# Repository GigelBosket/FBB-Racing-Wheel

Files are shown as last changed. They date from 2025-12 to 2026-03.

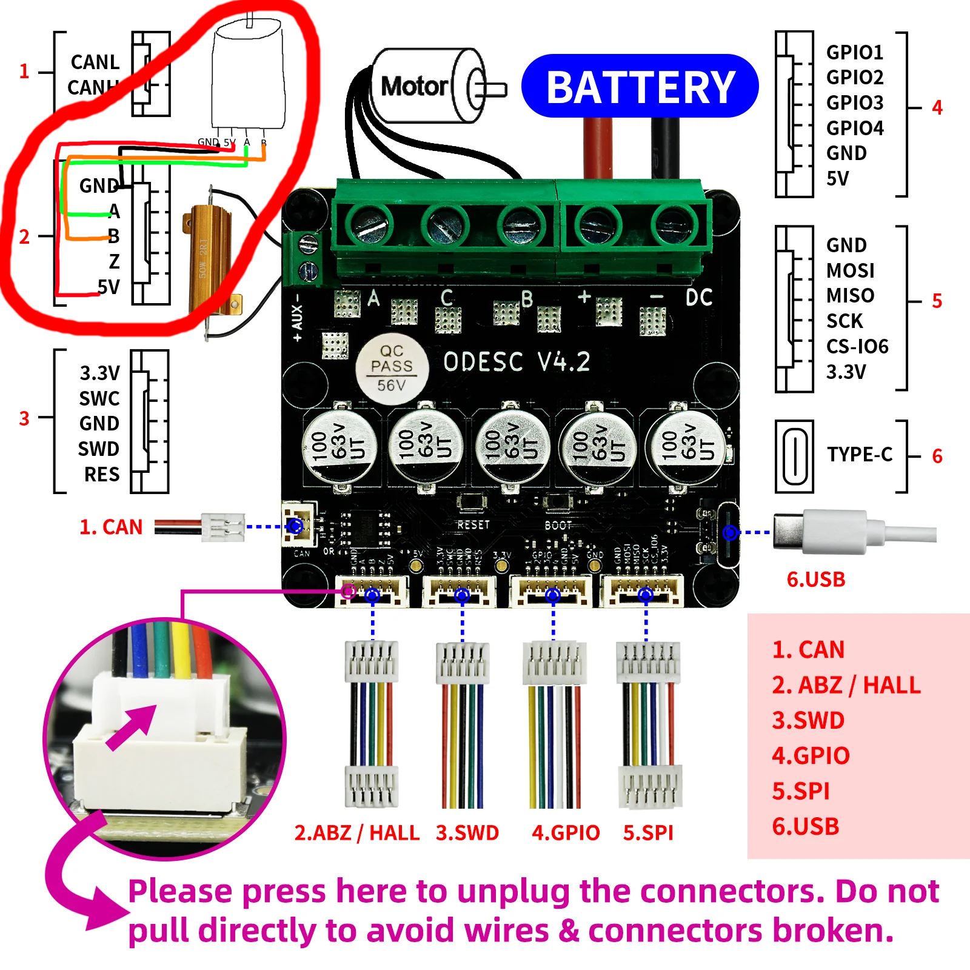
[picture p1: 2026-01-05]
images/ODESC V4.2 diagram.png

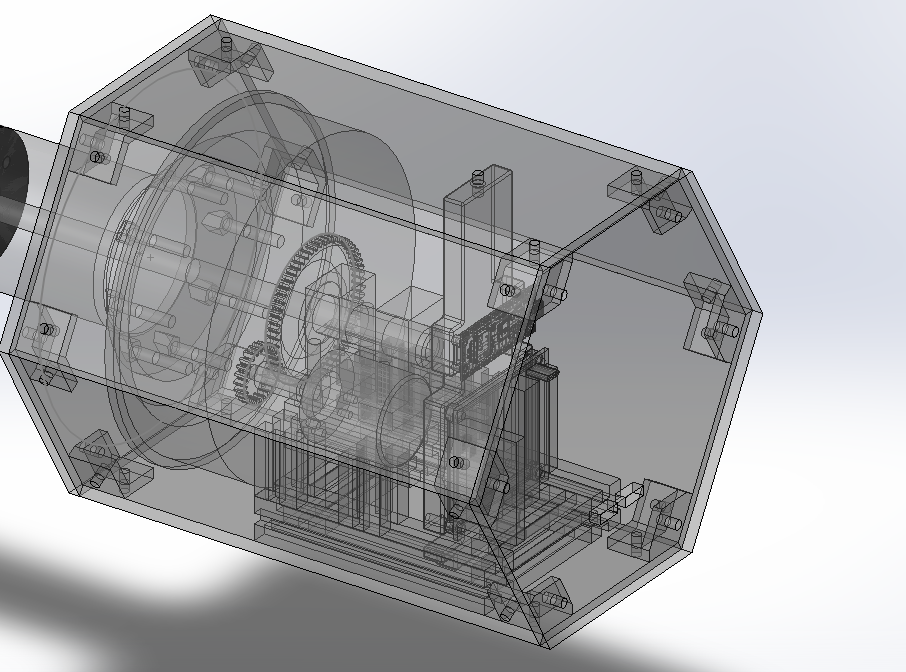
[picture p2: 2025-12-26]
images/Screenshot_1.png

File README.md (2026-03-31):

# FBB-Racing-Wheel
Custom Racing Wheel with Force Feedback containing the wheelbase and steering wheel with the attachments to connect the 2 together. A custom PCB will be used to control the hoverboard motor and read it's position throw a rotary encoder connected to the motor with 2 gears. A Pico 2 is used in the wheelbase to receive data from the wheel(which also has a pico 2) throw SPI protocol. The pico 2 isn't used only for receiving data from the steering wheel, it could also get data from other devices like pedals, shifter, handrbrake and many more. The pico 2 supports up to 6 SPI/I2C connections and also sensors can directly be connected to it's GPIO pins.

The big difference between my racing wheel and others is that mine has direct data transfer throw the magnetic pins from steering wheel to wheelbase which goes in the pc. That means very small latency and no cable twisting all thanks to the magnetic pins (pogo pins) and the slipring. The downside that comes with this is the plastic parts for the high strain parts like the motor extension and the quick release all from plastic(3d printed) but it still should work fine.

I'm making the project so I could inspire others with my design as it's different than most I've seen. And also it's way cheaper than buying a new one with similar specs.

**Specs:**
 - up to 15nm of torque
 - fast response time of 1ms(1000hz)
 - wheel base is  L=20cm, W=20cm(at the corner, max dist) H=17cm.
 - steering wheel is 33cm
 - the 3d printed case for the steering wheel L=16.2cm, W=3.2cm, H=7.5.
 - 12 buttons
 - 5 encoders
 - 1 funcky switch(for easier customization of the car in games/other actions like camera fix position)
 - high precision encoder(for motor)

Wheel final version below
Rendered_model

Wheel base


Close image from the steering wheel face


The back of the steering wheel 


Simple wiring scheme for the Pico 2 of the wheel base to the wires of the slip ring. The image also includes a simple connections from the pico 2 to some sensors if you want to directly connect any sensor to it.


Custom bldc motor driver PCB


PCB image of it's top copper layer


Steering wheel buttons/encoders will be connected to the pico 2 throw a matrix system in which each button is connected to column and row and the pico 2 will send a signal to each column and then wait for output from any of the rows and that's how it will find which buttons got pressed. This matrix system allows the usage of a high number of buttons without haveing a pin for each button. Also a diode will be used to prevent the current from flowing the opposite direction and causing ghosting. The order in which the buttons are connected doesn't matter so I won't include a photo of that. Also I won't add the file for schematic as it's a very simple schematic which isn't linked to other files and it's used to have and idea how the connections work for who doesn't already know(the wires can be connected to others pins and still work fine).Just don't forget to connect it to the pogo pins which then go to the Pico 2 in the wheel base which will process the data, don't forget to wire the pins accordingly for SPI protocol(example above). The pico 2 of the steering wheel is gonna be the slave while the pico in the base is gonna be the master. Slave awaits commands from master.

**Print tips**
So the parts used to connect the motor to the wheel should be printed with 95% infill, the oher parts should be printed with 15-30% infill as they won't have that much strain on them
I m gonna use ASA fillament as it is pretty strong and should do the job well.
Also if you are a total beginer you should download only the stl files as they are the only one needed to print the parts.

I used Raspberry Pi Pico extension in VS code which downloads the SDK for pico and other packages automaticly. If you want to use my code for Pico 2 just git clone my project then open the folder with the code you want to upload on your pico, in VS Code (after installing the extension) and just compile, select port of Pico 2 and upload.

Pico 2:



What you need to wire to the bldc motor driver PCB:
PCB small diagram

| BOM Total | | | Price in us dollars | | | |
|---|---|---|---|---|---|---|
| Material/Product | Quantity | Price per Unit | SubTotal | Shipping | TotalPrice | Link |
| HoverBoard Motor | 1 | 20 | 20 | 5 | 25 | Local Market(OLX.ro) |
| Pico 2 | 1 | 5.5 | 5.5 | 6 | 11.5 | https://www.tme.eu/ro/cart/step/0/order/33780296 |
| SK16 support | 2 | 5.5 | 11 | 5 | 16 | https://www.cnc-kit.ro/cumpara/sk16-suport-ax-16-mm-676 |
| Rotary Encoder 38S6G5-B-G24N | 1 | 11 | 11 | 5 | 16 | https://www.aliexpress.com/item/1005006657099269.html?spm=a2g0o.detail.0.0.48bfnCCMnCCMPD&mp=1 |
| MicroUsb convertor to Usb A | 1 | 0.35 | 0.35 | 0 | 0.35 | https://www.aliexpress.com/item/1005005982662099.html?spm=a2g0o.detail.0.0.771aF986F986OE&mp=1 |
| Usb C convertor to Usb A | 1 | 0.35 | 0.35 | 0 | 0.35 | https://www.aliexpress.com/item/1005005982662099.html?spm=a2g0o.detail.0.0.771aF986F986OE&mp=1 |
| Aluminium Profile 20mm x 1m | 1 | 8 | 8 | 5 | 13 | https://www.automatic.ro/profiluri-de-aluminiu/510-profil-de-aluminiu-20x20-mm-canal-5-tip-item.html |
| M4x10mm Screw | 48 | 0.04 | 1.92 | 0 | 1.92 | https://www.dedeman.ro/ro/surub-cu-cap-cilindric-cu-locas-hexagonal-otel-zincat-alb-din-912-8-8-sw-3-m4-x-10-mm/p/1033735 |
| M4 nuts | 48 | 0.012 | 0.576 | 0 | 0.58 | https://www.dedeman.ro/ro/piulita-hexagonala-din-otel-zincat-alb-din-934-m4/p/6000218 |
| M5 screw(pack of 5) | 1 | 3.62 | 3.62 | 0 | 3.62 | https://www.dedeman.ro/ro/surub-cu-cap-cilindric-cu-locas-hexagonal-otel-zincat-alb-din-912-8-8-m5-x-30-mm-set-5-bucati/p/6014463 |
| M5 nuts | 4 | 0.012 | 0.048 | 0 | 0.05 | https://www.dedeman.ro/ro/piulita-hexagonala-din-otel-zincat-alb-din-934-m5/p/6000211 |
| Slip Ring | 1 | 14 | 14 | 0 | 14 | https://www.aliexpress.com/item/1005007469166149.html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 |
| 6 pin magnetic connector(male and female) | 1 | 2 | 2 | 0 | 2 | https://www.aliexpress.com/item/1005010344872906.html?spm=a2g0o.productlist.0.0.23cd1f3eKvgHZs&mp=1 |
| Power Supply 24v 20A(80%efficiency) | 1 | 39 | 39 | 0 | 39 | https://www.aliexpress.com/item/33051556213.html?spm=a2g0o.cart.0.0.295838daYNvhOv&mp=1 |
| 12AWG Red and Black cable | 1 | 7 | 7 | 0 | 7 | https://www.aliexpress.com/item/1005008617874353.html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 |
| Steering Wheel | 1 | 59 | 59 | 3 | 62 | https://www.aliexpress.com/item/1005005748732216.html?spm=a2g0o.detail.0.0.771aF986F986OE&mp=1 |
| RKJXT1F42001 | 1 | 3.66 | 3.66 | 0 | 3.66 | https://www.aliexpress.com/item/1005006287472896.html?spm=a2g0o.cart.0.0.295838daYNvhOv&mp=1 |
| Push Button | 1 | 2.2 | 2.2 | 0 | 2.2 | https://www.aliexpress.com/item/1005001700262900.html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,scm-url:1007.40050.354490.0,pvid:ea68574a-2666-4e59-a2fa-c057ce48ff6b,tpp_buckets:668%232846%238108%231977&pdp_ext_f=%7B%22order%22%3A%2246%22%2C%22eval%22%3A%221%22%2C%22sceneId%22%3A%2230050%22%2C%22fromPage%22%3A%22recommend%22%7D&utparam-url=scene%3ApcDetailTopMoreOtherSeller%7Cquery_from%3A%7Cx_object_id%3A1005001700262900%7C_p_origin_prod%3A |
| Rotary encoders 15mm shaft(pack of 5) | 1 | 3.7 | 3.7 | 0 | 3.7 | https://www.aliexpress.com/item/32877104625.html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 |
| Knob of rotary encoders (pack of 10( | 1 | 1.4 | 1.4 | 0 | 1.4 | https://www.aliexpress.com/item/1005006995837493.html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 |
| M6 x60mm screw | 6 | 0.17 | 1.02 | 0 | 1.02 | https://www.dedeman.ro/ro/surub-cu-cap-hexagonal-filetat-complet-otel-zincat-alb-m6-x-60-mm/p/6000728 |
| M6 nuts | 6 | 0.032 | 0.192 | 0 | 0.19 | https://www.dedeman.ro/ro/piulita-hexagonala-cu-autoblocare-din-otel-din-985-8-m6/p/6006481 |
| M3 x16mm screw(pack of 20) | 1 | 0.86 | 0.86 | 0 | 0.86 | https://www.dedeman.ro/ro/surub-cu-cap-bombat-amprenta-cruce-cu-piulita-easy-fix-otel-zincat-alb-m3-x-16-mm-set-20-bucati/p/6014509 |
| 1N4148 | 25 | 0.247 | 6.175 | 0 | 6.18 | https://www.tme.eu/ro/details/1n4148-dio/diode-universale-tht/diotec-semiconductor/1n4148/ |
| 28AWG Black Cable | 2 | 0.5 | 1 | 0.7 | 1.7 | https://www.aliexpress.com/item/1005008612186010.html?spm=a2g0o.cart.0.0.295838daYNvhOv&mp=1 |
| 28AWG Red Cable | 2 | 0.5 | 1 | 0 | 1 | https://www.aliexpress.com/item/1005008612186010.html?spm=a2g0o.cart.0.0.295838daYNvhOv&mp=1 |
| PCB(min 5 Q) | 1 | 7 | 7 | 3.12 | 10.12 | |
| PCB BOM(for 1 board) | 1 | 32 | 32 | 9.52 | 41.52 | |
| | | | | | | |
| | | | | | | |
| | | | 243.57 | 42.34 | 285.92 | 

**PCB BOM**
Price is around 23 euros for parts only on LCSC website + other fees.
| Designator | Footprint | Quantity | Value | LCSC Part # |
|---|---|---|---|---|
| 50W RESISTOR | DEGSON DG381-3.5-02P-14-00A(H) | 1 | DEGSON DG381-3.5-02P-14-00A(H) | C5272864 |
| C1, C12, C2, C23, C29, C30, C33, C39, C4, C40, C5, C6, C7, C8 | 402 | 14 | 100nF | C1525 |
| C10, C11, C3, C9 | 402 | 4 | 4.7uF | C23733 |
| C13, C20, C24, C25 | 805 | 4 | 22uF | C711104 |
| C14, C15, C16, C19, C27 | 603 | 5 | 1uF | C15849 |
| C17, C18 | 402 | 2 | 15pF | C161530 |
| C21, C22, C31, C32, C34 | 805 | 5 | 10uF | C440198 |
| C26 | 603 | 1 | 100nF | C1591 |
| C28 | 603 | 1 | 47nF | C1622 |
| C35, C36, C37, C38 | CAP_EEEFK1H221P | 4 | 220uF | C72499 |
| D1 | D_SMC | 1 | SMCJ30A | C4154618 |
| D10 | 402 | 1 | LED | C434446 |
| D2 | D_SMA | 1 | SS14 | C2837270 |
| J1 | USB_C_Receptacle_G-Switch_GT-USB-7051x | 1 | USB_C_Receptacle_USB2.0_16P | C2843970 |
| J3 | JST_SH_BM05B-SRSS-TB_1x05-1MP_P1.00mm_Vertical | 1 | Encoder  Port | C160391 |
| J4 | DORABO DB128V-5.08-5P-GN-S | 1 | DB128V-5.08-5P-GN-S | C2927513 |
| L1 | AOTA-B201610S3R3-101-T | 1 | 3.3uH | C42411119 |
| L2 | VLS6045EX-4R7M-H | 1 | 4.7 uH | C360735 |
| L3 | IND_ETQP4M220KVK | 1 | ETQP4M220KVK | C542324 |
| Q1, Q2, Q3, Q4, Q5, Q6 | TDSON-8-1 | 6 | CSD18532Q5B | C882766 |
| Q7 | SOT-23 | 1 | IRLZ44N(UMW) | C42370423 |
| R1, R5, R6 | 402 | 3 | 33 | C25105 |
| R13, R14, R15, R4, R7 | 402 | 5 | 1k | C11702 |
| R16, R19, R29, R31 | 402 | 4 | 10k | C25744 |
| R18 | 402 | 1 | 100k | C25741 |
| R2, R3 | 402 | 2 | 5k1 | C25905 |
| R20, R21, R22 | 2512 | 3 | 5M1 | C419720 |
| R30 | 402 | 1 | 31k6 | C11463 |
| R8, R9 | 402 | 2 | 27 | C278580 |
| S1 | SW_TL3365AF180QG | 1 | TL3365AF180QG | C2886926 |
| U1 | QFN-48-1EP_7x7mm_P0.5mm_EP5.3x5.3mm | 1 | DRV8323RSRGZR | C545497 |
| U2 | QFN-60-1EP_7x7mm_P0.4mm_EP3.4x3.4mm | 1 | RP2354A | C41378174 |
| U3 | TSOT-23-6 | 1 | AP63203WU | C780769 |
| Y2 | XTAL_ABM8-272-T3 | 1 | ABM8-272-T3 | C20625731 |

The next 2 BOMS are an aproximation for how much for just one of them. It is not 100% accurate

|Wheelbase | | | | |Price in US dollars| |
|---|---|---|---|---|---|---|
|Material/Product |Quantity|Price per Unit|SubTotal |Shipping |TotalPrice |Link |
|HoverBoard Motor |1 |20 |20 |5 |25 |Local Market(OLX.ro) |
|Pico 2 |1 |5.5 |5.5 |6 |11.5 |[link](https://www.tme.eu/ro/cart/step/0/order/33780296) |
|SK16 support |2 |5.5 |11 |5 |16 |[link](https://www.cnc-kit.ro/cumpara/sk16-suport-ax-16-mm-676) |
|Rotary Encoder 38S6G5-B-G24N |1 |11 |11 |5 |16 |[link](https://www.aliexpress.com/item/1005006657099269.html?spm=a2g0o.detail.0.0.48bfnCCMnCCMPD&mp=1) |
|MicroUsb convertor to Usb A |1 |0.35 |0.35 |0 |0.35 |[link](https://www.aliexpress.com/item/1005005982662099.html?spm=a2g0o.detail.0.0.771aF986F986OE&mp=1) |
|Usb C convertor to Usb A |1 |0.35 |0.35 |0 |0.35 |[link](https://www.aliexpress.com/item/1005005982662099.html?spm=a2g0o.detail.0.0.771aF986F986OE&mp=1) |
|Aluminium Profile 20mm x 1m |1 |8 |8 |5 |13 |[link](https://www.automatic.ro/profiluri-de-aluminiu/510-profil-de-aluminiu-20x20-mm-canal-5-tip-item.html) |
|M4x10mm Screw |48 |0.04 |1.92 |0 |1.92 |[link](https://www.dedeman.ro/ro/surub-cu-cap-cilindric-cu-locas-hexagonal-otel-zincat-alb-din-912-8-8-sw-3-m4-x-10-mm/p/1033735) |
|M4 nuts |48 |0.012 |0.576 |0 |0.58 |[link](https://www.dedeman.ro/ro/piulita-hexagonala-din-otel-zincat-alb-din-934-m4/p/6000218) | |
|M5 screw(pack of 5) |1 |3.62 |3.62 |0 |3.62 |[link](https://www.dedeman.ro/ro/surub-cu-cap-cilindric-cu-locas-hexagonal-otel-zincat-alb-din-912-8-8-m5-x-30-mm-set-5-bucati/p/6014463) |
|M5 nuts |4 |0.012 |0.048 |0 |0.05 |[link](https://www.dedeman.ro/ro/piulita-hexagonala-din-otel-zincat-alb-din-934-m5/p/6000211) |
|Slip Ring |1 |14 |14 |0 |14 |[link](https://www.aliexpress.com/item/1005007469166149.html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) |
|6 pin magnetic connector(male and female)|1 |2 |2 |0 |2 |[link](https://www.aliexpress.com/item/1005010344872906.html?spm=a2g0o.productlist.0.0.23cd1f3eKvgHZs&mp=1) |
|Power Supply 24v 20A(80%efficiency) |1 |39 |39 |0 |39 |[link](https://www.aliexpress.com/item/33051556213.html?spm=a2g0o.cart.0.0.295838daYNvhOv&mp=1) |
|12AWG Red and Black cable |1 |7 |7 |0 |7 |[link](https://www.aliexpress.com/item/1005008617874353.html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)
| | | | | | | |
| | | | | | | |
| | | |151.36  |31 |181.37 | |

|Steering Wheel | | | | |Price in us dollars| |
|---|---|---|---|---|---|---|
|Materials/Products |Quantity|Price per Unit|SubTotal|Shipping|Total Price |Links |
|Steering Wheel |1 |59 |59 |3 |62 |[link](https://www.aliexpress.com/item/1005005748732216.html?spm=a2g0o.detail.0.0.771aF986F986OE&mp=1) |
|RKJXT1F42001 Multi-function switch |1 |3.66 |3.66 |0 |3.66 |[link](https://www.aliexpress.com/item/1005006287472896.html?spm=a2g0o.cart.0.0.295838daYNvhOv&mp=1) |
|Push Button Switch with caps(pack of 50)|1 |2.2 |2.2 |0 |2.2 |[link](https://www.aliexpress.com/item/1005001700262900.html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,scm-url:1007.40050.354490.0,pvid:ea68574a-2666-4e59-a2fa-c057ce48ff6b,tpp_buckets:668%232846%238108%231977&pdp_ext_f=%7B%22order%22%3A%2246%22%2C%22eval%22%3A%221%22%2C%22sceneId%22%3A%2230050%22%2C%22fromPage%22%3A%22recommend%22%7D&utparam-url=scene%3ApcDetailTopMoreOtherSeller%7Cquery_from%3A%7Cx_object_id%3A1005001700262900%7C_p_origin_prod%3A)|
|Rotary encoders 15mm shaft(pack of 5) |1 |3.7 |3.7 |0 |3.7 |[link](https://www.aliexpress.com/item/32877104625.html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) |
|Knob of rotary encoders (pack of 10( |1 |1.4 |1.4 |0 |1.4 |[link](https://www.aliexpress.com/item/1005006995837493.html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) |
|M6 x60mm screw |6 |0.17 |1.02 |0 |1.02 |[link](https://www.dedeman.ro/ro/surub-cu-cap-hexagonal-filetat-complet-otel-zincat-alb-m6-x-60-mm/p/6000728) |
|M6 nuts |6 |0.032 |0.192 |0 |0.19 |[link](https://www.dedeman.ro/ro/piulita-hexagonala-cu-autoblocare-din-otel-din-985-8-m6/p/6006481) |
|M3 x16mm screw(pack of 20) |1 |0.86 |0.86 |0 |0.86 |[link](https://www.dedeman.ro/ro/surub-cu-cap-bombat-amprenta-cruce-cu-piulita-easy-fix-otel-zincat-alb-m3-x-16-mm-set-20-bucati/p/6014509) |
|Pico 2 |1 |5.5 |5.5 |0 |5.5 |[link](https://www.tme.eu/ro/details/sc1631/raspberry-pi-sisteme-incorporate/raspberry-pi/raspberry-pi-pico-2/) | |
|1N4148 |25 |0.247 |6.175 |0 |6.18 |[link](https://www.tme.eu/ro/details/1n4148-dio/diode-universale-tht/diotec-semiconductor/1n4148/) |
|28AWG Black Cable |2 |0.5 |1 |0.7 |1.7 |[link](https://www.aliexpress.com/item/1005008612186010.html?spm=a2g0o.cart.0.0.295838daYNvhOv&mp=1) |
|28AWG Red Cable |2 |0.5 |1 |0 |1 |[link](https://www.aliexpress.com/item/1005008612186010.html?spm=a2g0o.cart.0.0.295838daYNvhOv&mp=1) |
| | | | | | | |
| | | | | | | |
| | | |100.21 |3.7 |103.91 | |

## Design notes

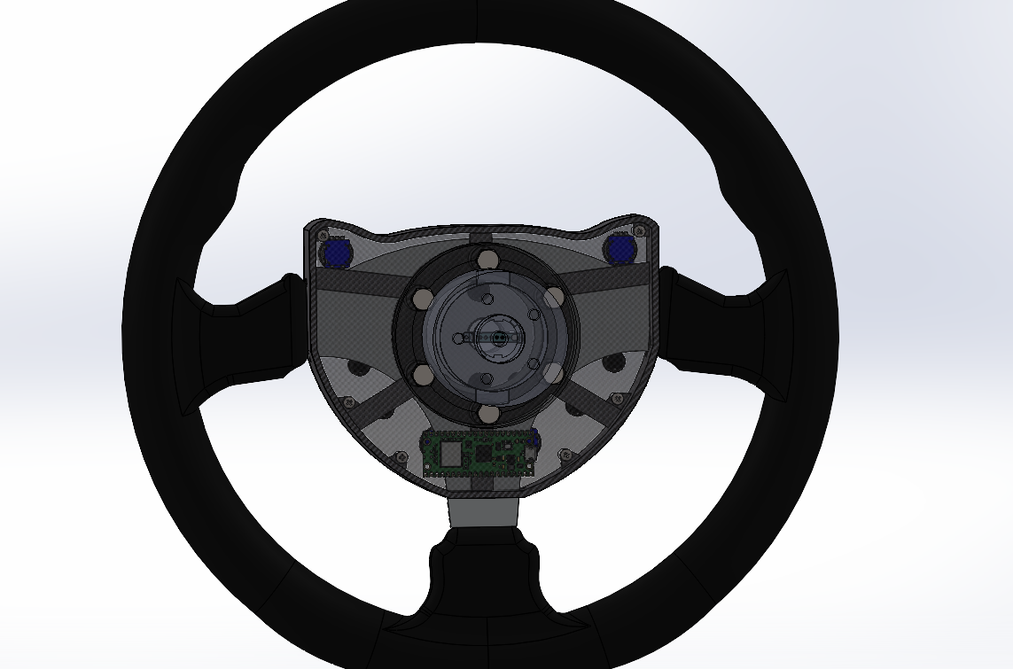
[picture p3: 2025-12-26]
images/Screenshot_3.png

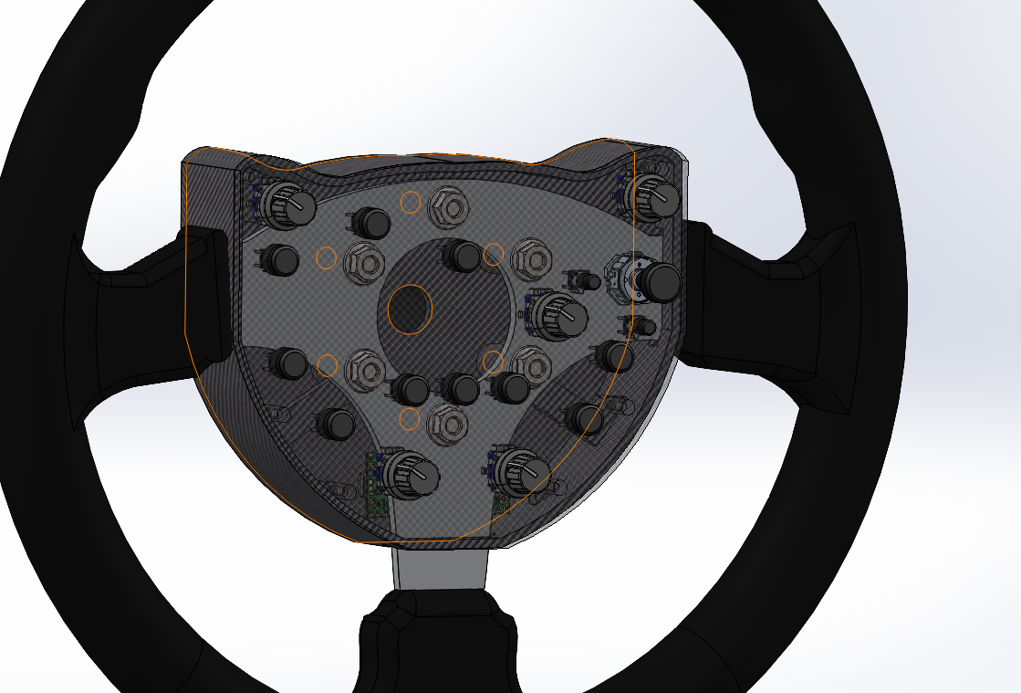
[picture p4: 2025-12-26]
images/Screenshot_2.png

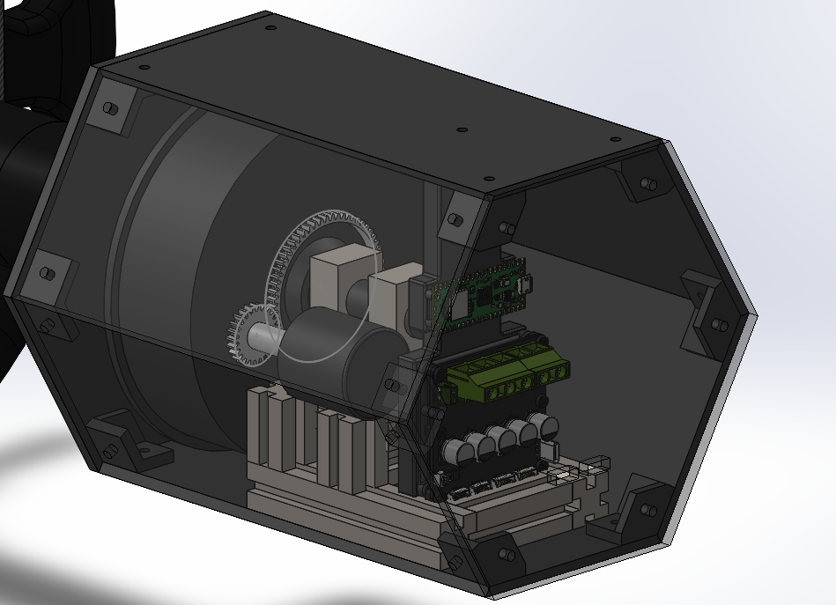
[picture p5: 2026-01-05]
images/Screenshot_4.png

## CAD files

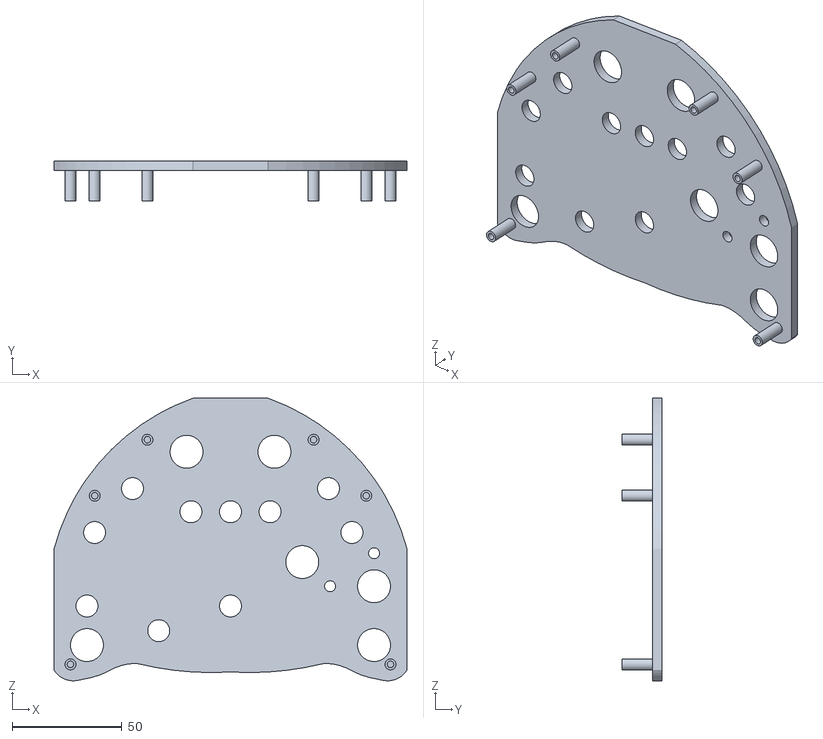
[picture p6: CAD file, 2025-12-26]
CAD/STL/SteeringWheel/Wheel front face.STL
160.7 x 18.2 x 128.7

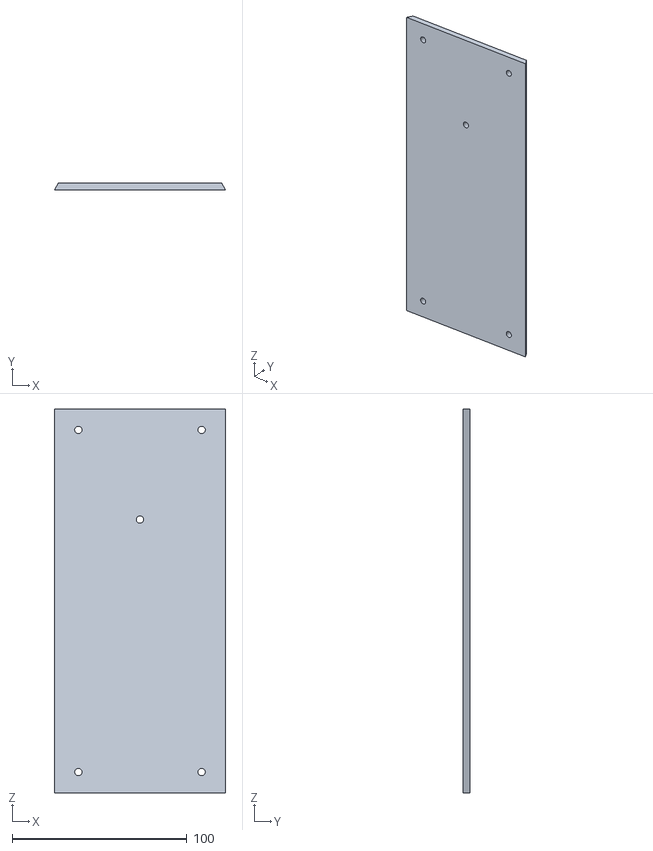
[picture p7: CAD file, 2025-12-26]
CAD/STL/WheelBase/Top plate.STL
98.2 x 4.00 x 220.0

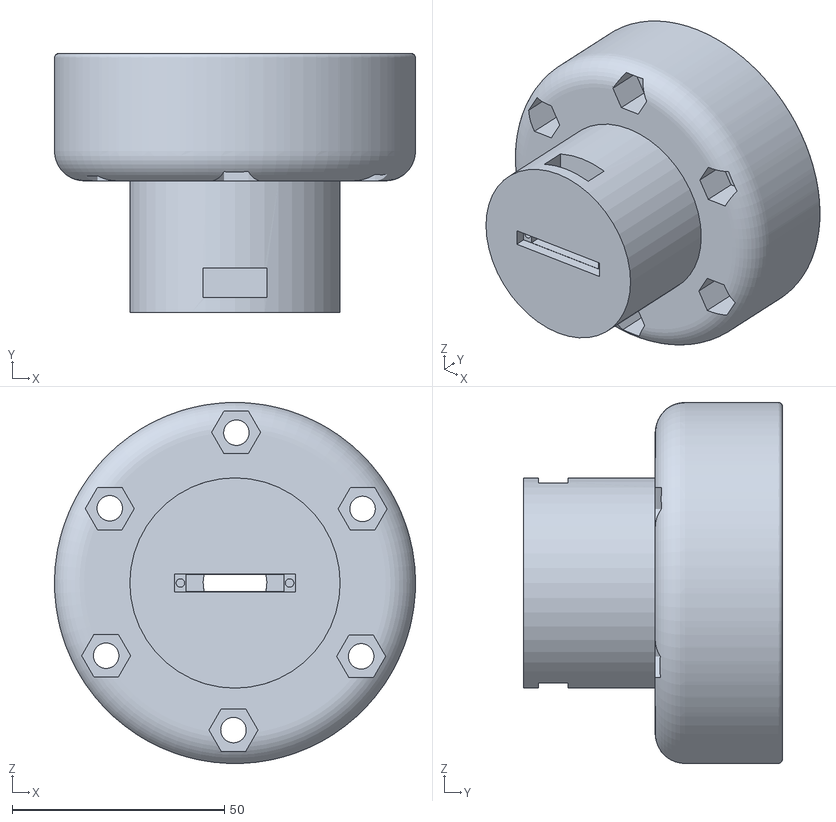
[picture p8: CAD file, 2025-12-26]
CAD/STL/SteeringWheel/wheel attachement.STL
85.0 x 61.0 x 85.0

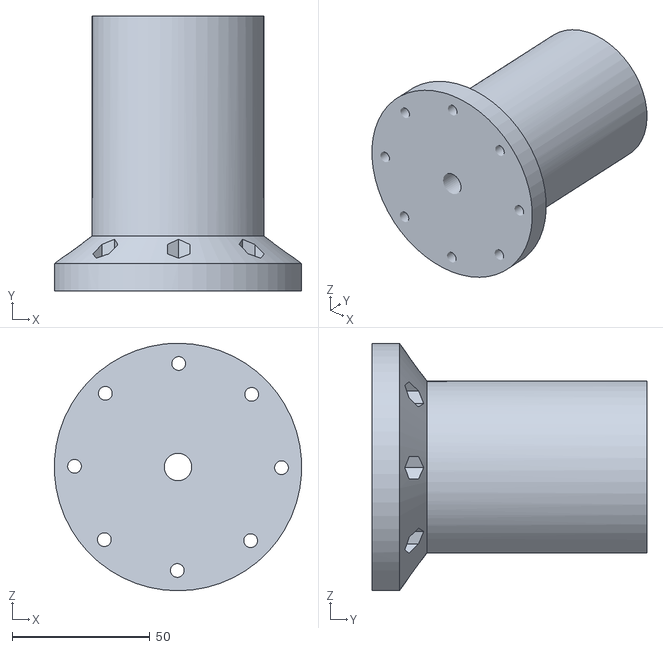
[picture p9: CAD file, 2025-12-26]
CAD/STL/WheelBase/Motor attachment.STL
89.8 x 100.0 x 90.0

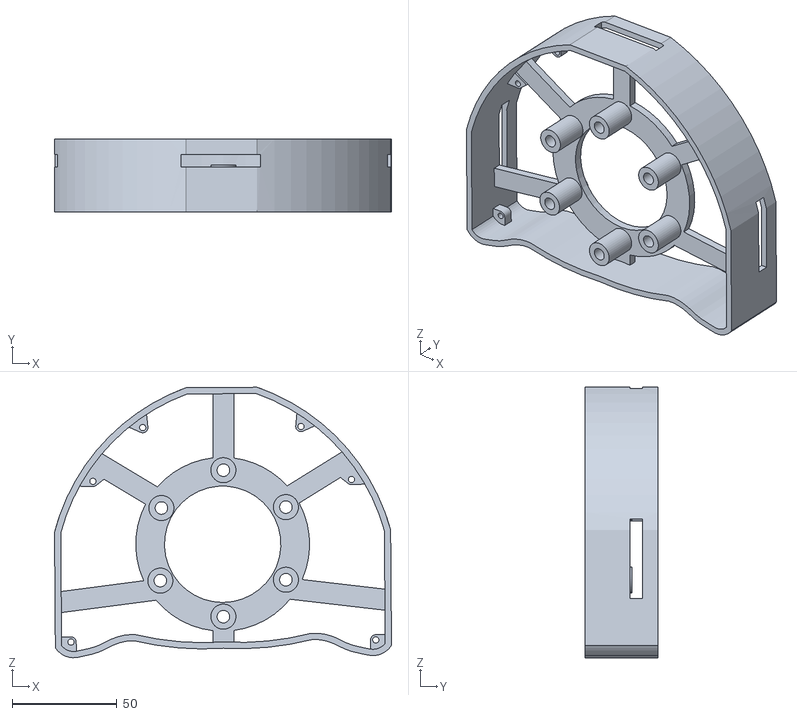
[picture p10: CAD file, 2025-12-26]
CAD/STL/SteeringWheel/Wheel middle part.STL
161.1 x 35.0 x 129.3

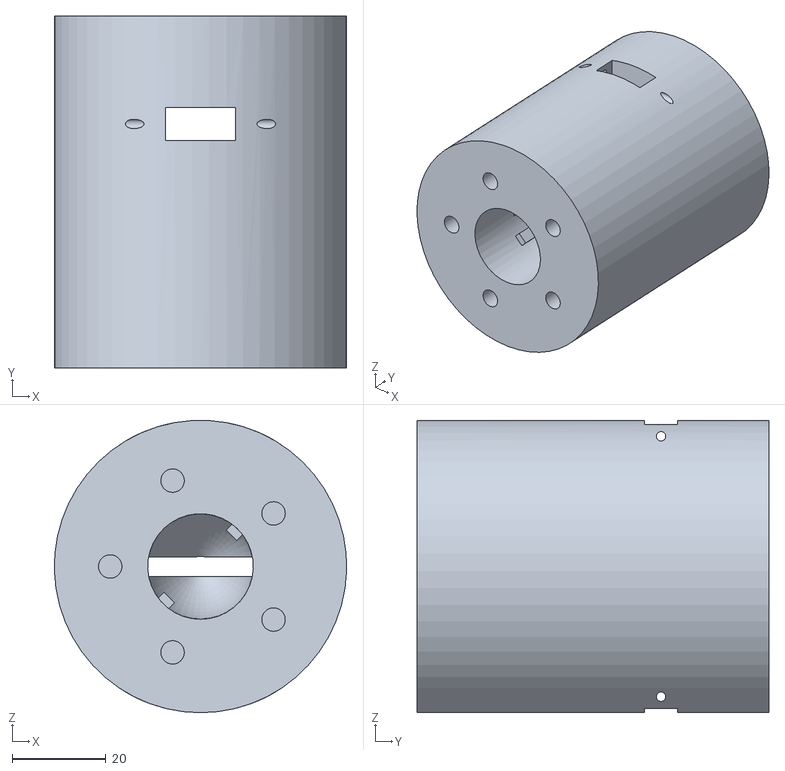
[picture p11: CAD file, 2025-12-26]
CAD/STL/WheelBase/Quick release support.STL
62.3 x 75.0 x 62.3

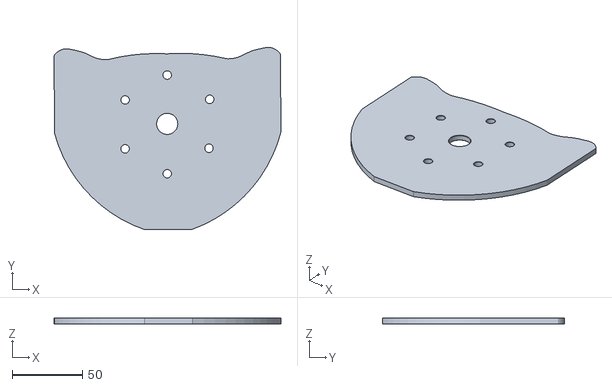
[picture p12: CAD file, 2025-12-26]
CAD/STL/SteeringWheel/Wheel back panel.STL
161.1 x 129.3 x 4.00

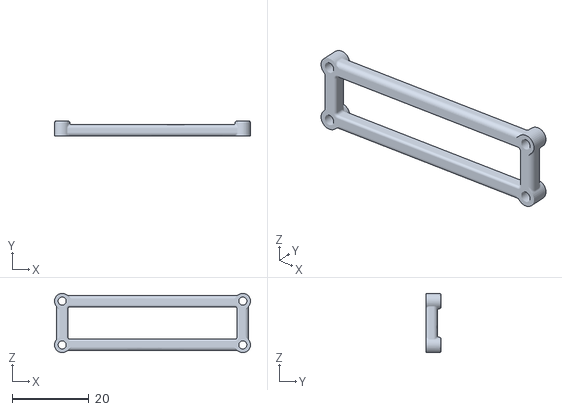
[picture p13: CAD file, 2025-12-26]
CAD/STL/WheelBase/Pico2 support.STL
51.0 x 4.00 x 15.4

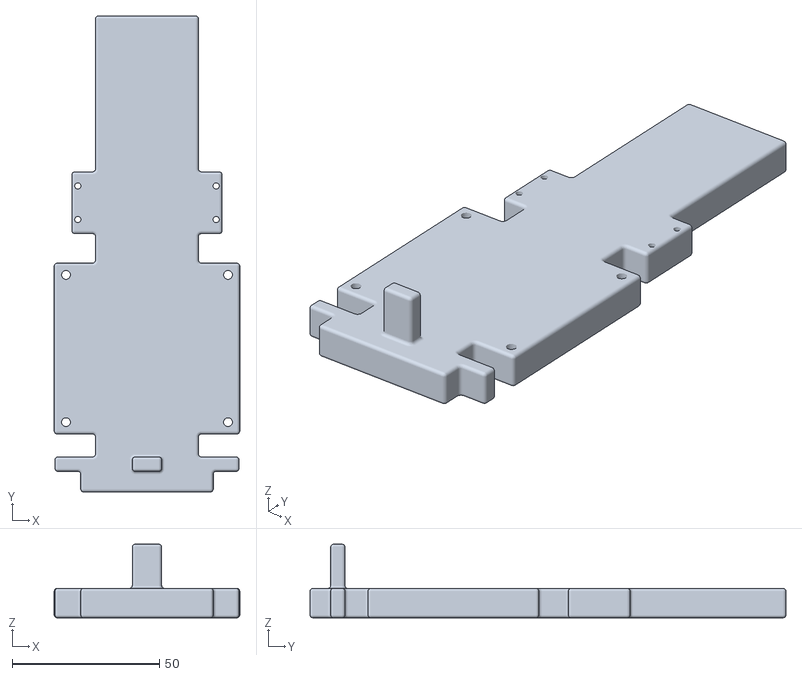
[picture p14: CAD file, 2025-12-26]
CAD/STL/WheelBase/Pcb vertical support.STL
63.0 x 161.6 x 25.0

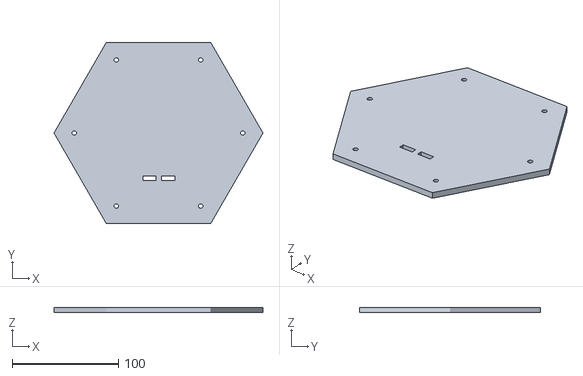
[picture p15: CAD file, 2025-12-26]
CAD/STL/WheelBase/black_Plate.STL
196.3 x 170.0 x 5.00

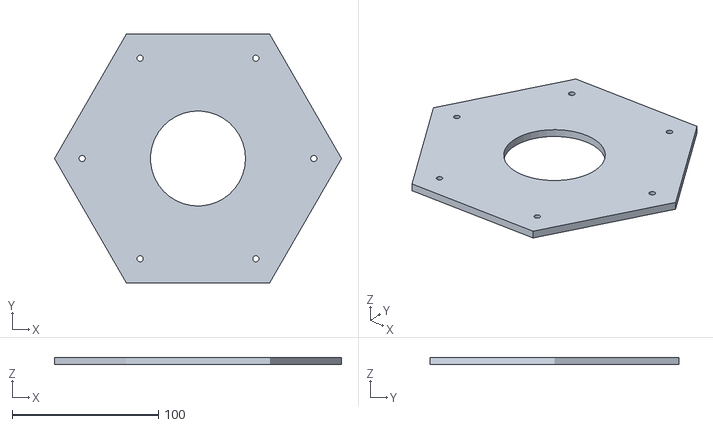
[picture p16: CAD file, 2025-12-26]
CAD/STL/WheelBase/front_Plate.STL
196.3 x 170.0 x 5.00

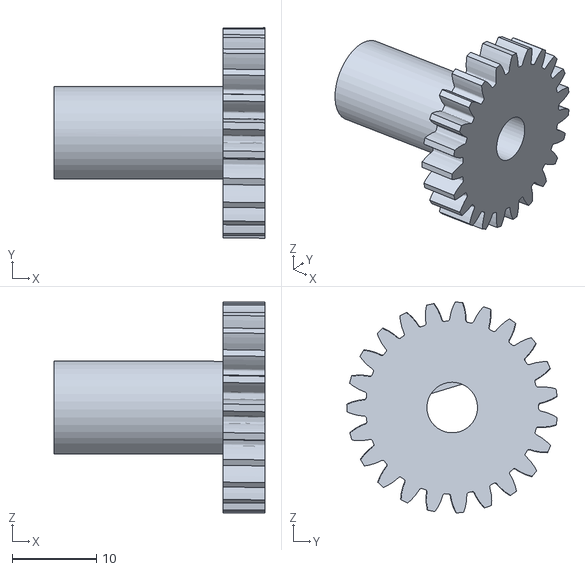
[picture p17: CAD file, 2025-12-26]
CAD/STL/WheelBase/small gear.STL
25.0 x 24.9 x 25.0

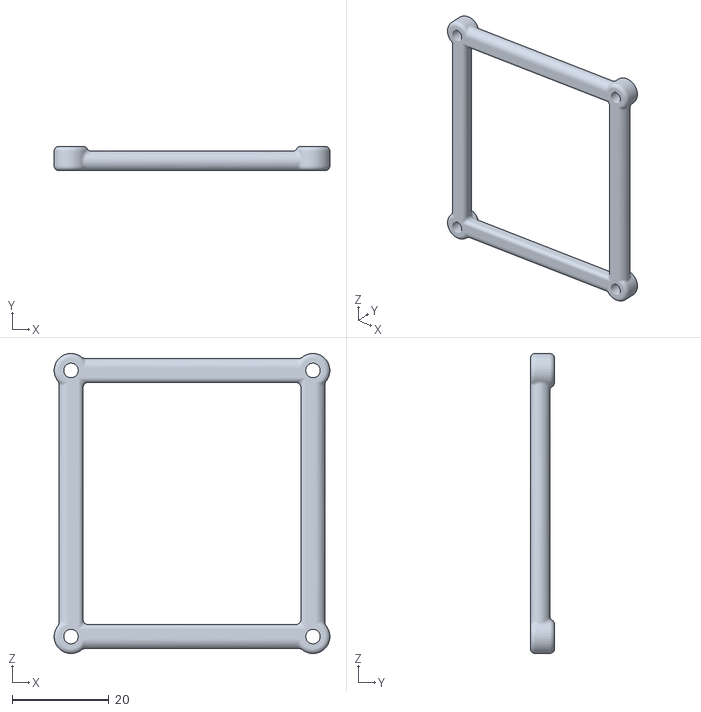
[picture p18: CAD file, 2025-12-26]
CAD/STL/WheelBase/ODSEC SUPPORT.STL
57.0 x 5.00 x 62.0

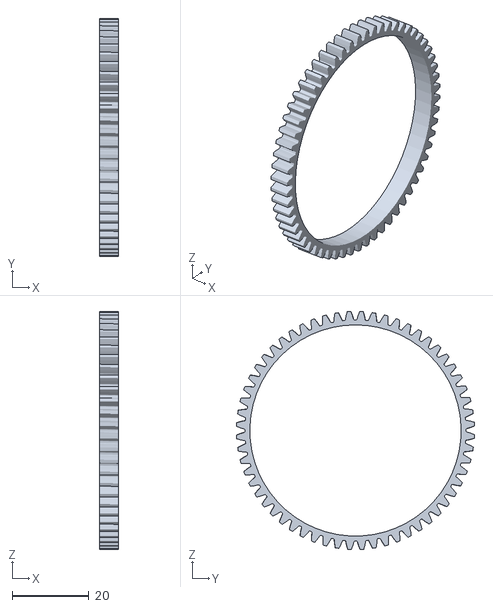
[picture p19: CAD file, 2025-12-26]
CAD/STL/WheelBase/big gear.STL
5.00 x 62.0 x 62.0

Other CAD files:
CAD/STEP/WheelBase-and-SteeringWheel.STEP
CAD/STL/WheelBase/lateral_Plate.STL
CAD/STL/WheelBase/Corner screw support.STL

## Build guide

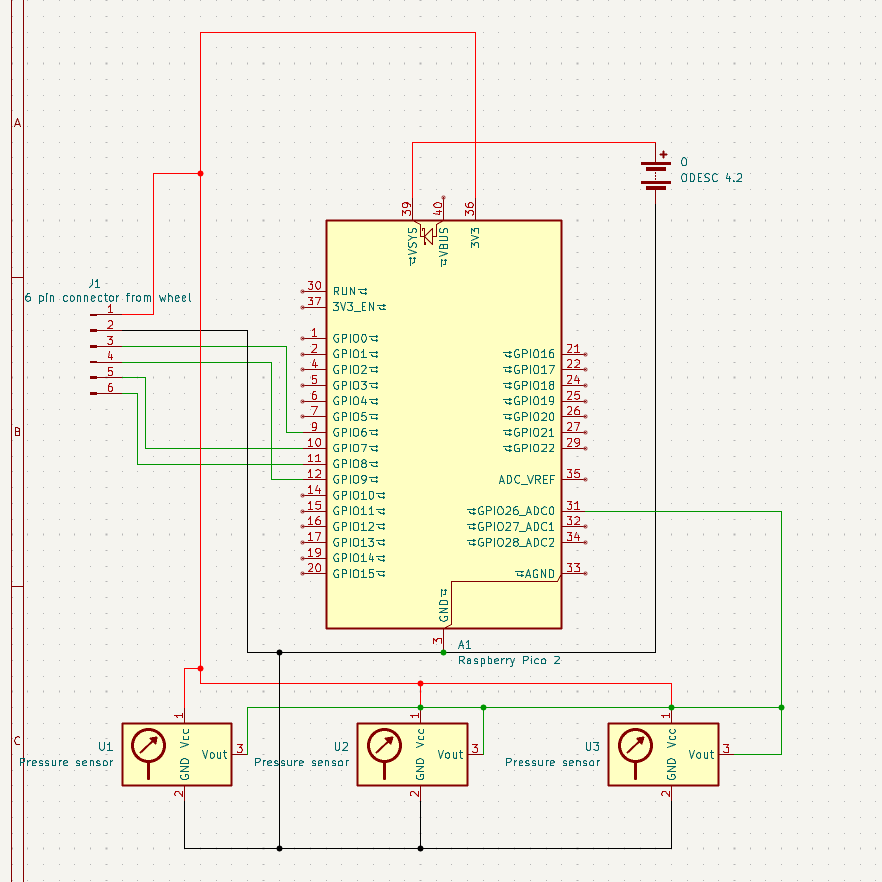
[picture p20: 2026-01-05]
images/Pico 2 wiring to SPI and aux sensors.png

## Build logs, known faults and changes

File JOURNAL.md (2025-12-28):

# Total Time Spent: 87 Hours

## Date: 12/7/2025
## Time Spent: 25 Hours
(note: at the moment I had very little experience with the cad and everything took a lot as I encountered problems, and the documentation was very little as I only later read the requiremets to document around every 5 hours)
### Designed motor attachments 
**I designed the hoverboard motor which I will use in my wheelbase as well as some attachments for it.**

**The attachments consists of:** 
	**1**. a part which will be screwed in the motor and secures a good connection between the motor and the slip ring support.
	**2**. a slip ring support which also has the mounting holes for the wheel it self. This slip ring support will fit a slip ring which will prevent the wires from twisting and also a magnetic pogo pin female for a quick release.
	After watching others DIY wheels I saw that every one was simple with no wheel buttons or a usb on the wheel, which made experience worse in my opinion. So I tried to resolve those problems on my own. So I did some research, I watched at some great wheels from moza and trustmaster and I saw they use some pins and pads to make the connections but when I thought I got it than I realised that the wires will twist if I don't do anything but just connect them straight, and so I had an idea to make a circle from a conductive material and than have a still wire which will make the connections but that of course will fail cuz of the friction and sometimes bad contact but then I found out there is a thing named slip ring which does exactly what I wanted and it's reliable for long term use.
	Right now I m still thinking if I should also send the signal from the wheel to wheel base throw the wires or send it wireless and use the wires just for power alimentation. But I added a 6 wires slip ring with max 2Amp just in case if I will want to send the signal throw wires.
	

## Date: 12/18/2025
## Time Spent: 18 Hours
### Designed the motor cover case + most of the parts
I designed the motor base case with hexagonal front-back plates and some panels for each margin of the hexagon. I got the idea from the Thrustmaster t818.<br/><br/>

So I have some sk16 metal supports which will hold the metal axis of the hoverboard motor, so the motor can spin freely with the front support of the wheel.

A rotary encoder will be used to get the exact position of the motor using 2 gears, one glued to the motor cover and one on the shaft of the encoder.

Everything will be attached to some aluminium profile of 20mm and probably a few parts of 15mm profile

Also there is a vertical support made of plastic for the pcb.<br/><br/>

Previously I wanted to make a custom pcb but that will take a lot to design as my experience making pcb is very low. So I decided to use a bldc motor driver(probably a ODESC V4.2 but I m still researching) but I don't know how I m gonna support pedals with that and also connecting to pc might be a small problem. This took less time than the previous post as I learned to use a cad while working on this project.


## Date:12/21/2025
## Time Spend: 8 Hours
### Chose which boards to use + added them in the 3d model
So after some researched I found a great board for controlling the motor which has an stm32 and seems pretty powerful. The board is ODESC V4.2 24v which is based on an open source project and can be found for a bit under $30.

The power supply will be connected to the ODESC which will run on 24v. The board will output power to the brushless motor throw 3 wires. Also the board will receive input throw 2 wires as A and B from the rotary encoder to read the motor movement so it can transfer the movement in game.

And because I want to have buttons and maybe in the future even a screen on the wheel, I have to send that to the computer somehow. The transfer of information from the wheel to pc is handled by a Pico 2 which receive the data from the wheel throw SPI protocol and the data from the pedals directly throw analog. After the Pico 2 get's the data it will send it to the pc using TinyUSB library. So the Pico will get detected by windows as and HID(Human Interface Devices) which will act as a controller.

I made supports for the ODESC V4.2 and Pico 2 which will be screwed into the vertical support. Because the usb ports are not where they should be, in the back, I will probably use some usb extensions to keep everything clean.





## Date: 12/22/2025
## Time Spent: 6 Hours
### Making the steering wheel
Before starting to work on the steering wheel I thought it would be pretty easy but now that I m working on it I changed my opinion. I had so many problems with the shape as a well isn't completely round and smooth, it also has some shapes that help you get more grip, and those shapes are harder to make for somebody will limited experience like me.

Firstly I tried to make a 2d sketch with everything the wheel has, extrude and then just fillet but that didn't work.


So then I tried with loft extrude which was also bugging because of a shape.


That's the current wheel->

I will stop modeling useless things that doesn't help me or anyone. The wheel will be bought from aliexpress but I wanted to model the whole wheel as I need to make the box with the buttons and the raspberry/arduino which willbe atached with screws into the wheel.

## Date:12/23/2025
## Time Spent: 4.5 Hours
### Making the button layout
So far I made the shape of the button box in sketch and I almost finished the button layout.

I will mainly use 10mm buttons ,a few 15mm encoders, 2 5mm buttons for menu and back and in the final an encoder which also can tilt in 4 directions, rotate(left/right) and also push(I saw them on some more expensive wheels and I liked them so I added one to my wheel)


## Date: 12/24/2025
## Time Spent: 3.5 Hours
### Added the buttons to the wheel
I added a few buttons of 10mm and 5mm, rotary encoders with knobs and a encoder that moves in 4 directions as well of rotating (left right) which can be pressed like a button.(The buttons rotary encoders, and the 4d encoder 3d models I found online, the only thing I had to model was the buttons caps)

I added some textures so I could see better how the wheel will look in the reality with this shape and buttons.



## Date: 12/25/2025
## Time Spent: 7 Hours
### Made the wheel attachment and the the side part
So I made the part that will cover the sides with all the screw holders it needs in order to connect with the front plate which has the buttons.

Also made the wheel attachment and back plate. The wheel attachment will slide and lock with the part from the wheel base where the quick release is. I still have to model the quick release for the wheel attachment.

To hold the big strain I will use m6 hexagonal head screw of 60mm length in order to hold the wheel attachment and the wheel together. And m3 screws of 12mm to hold the plates together.






## Date: 12/25/2025
## Time Spent: 0.5 Hours
###Nuts and screws overlap with buttons
Just a quick update: 3 nuts and 1 screw overlaps with 3 buttons. It's not hard no repair but I just wanted to let you know about that, that's why I modeled more than I should and it took way longer than it should.


UPDATE 2: I fixed them by moving each by a few milimeters.


## Date: 12/26/2025
## Time Spent: 2.5 Hours
###Made Bill Of Materials
The Bill Of Materials took longer than expected but it's finally done. It took longer because some parts were unavailable/out of stock or their price has increased on the sites I looked initially.

Also the overall price is higher than expected because the currency exchange rate has changed quite a bit.

So I have to change the tier of the project to tier 1 from tier 2


## Date: 12/27/2025
## Time Spent: 4 Hours
###Added cad files and BOM to github
I exported the assembly file with the whole project together with step file(which took a long time to export) and the STL file for each part that has to be 3d printed.

Updated the BOM as I forgot a few things including power supply and some wires.



### Note: I saw I have to write how much I spend each day but I can't remember. Until 20 december I had school and each day from monday to friday I worked around 2 hours(to this project) per day and in the weekends some times even 10-12 hours but I didn't include that because I was working pretty slow and inefficient.

## Date: 12/28/2025
## Time Spent: 1 Hour
### 3D settings and planning for the print
So after speaking with a friend that has a 3d printer I will be making the parts from ASA because it's strong and easy to print and the failed parts number will be very low (hopefully 0)

The parts that connect the motor to the steering wheel are gonna be made with 95% infill as they will have some strain on them. Other parts will be printed with 15-30% depending on how much weight or strain will support each.

The full print will weight around 2.1 kg (quite a lot) but it will resist all the strain and weight.


## Date: 12/28/2025
## Time Spent: 3 Hours
### Wrote the code for Wheel Pico 2
So I wrote the code for the Wheel pico 2 in c++ using the raspberry pi pico SDK downloaded as an extension for VS Code.

Core 1 will read the buttons and encoders while core 0 will get that data and send it as a struct to the Pico 2 of the wheelbase throw SPI protocol. The pico 2 of the wheel will act as a slave while the pico 2 of the wheelbase will act as a Master.

I had some small problems with cmake as I mostly wrote code for arduino devices using PlatformIO, and when I was making c++ programs for windows I never bothered to learn c++. But I solved it pretty easy with some tutorials.

I used gemini a bit because I had some questions as writing code with this SDK is a bit different than what I was used.

In the final the code compiled and will be tested after I buy the pico 2.


## Date: 12/29/2025
## Spent Time: 4 Hours
### Wrote the code for pico 2 of the base to act as Controller
Wrote the code for the pico 2 of the wheel base to act as a Controller (HID) when connected to a pc.

I used TinyUSB library to make the communication between the pico 2 and the pc which was easier than I expected. I use some calls throw SPI protocol to get the data from the pico 2 in the wheel every 5 miliseconds.

In the feature I will also add support for pedals, shifter and other devices but for now I made only what I will need for this project.

I don't have a pico 2(as I mentioned previously) to test it on but it compiled and I hope it works in real life.


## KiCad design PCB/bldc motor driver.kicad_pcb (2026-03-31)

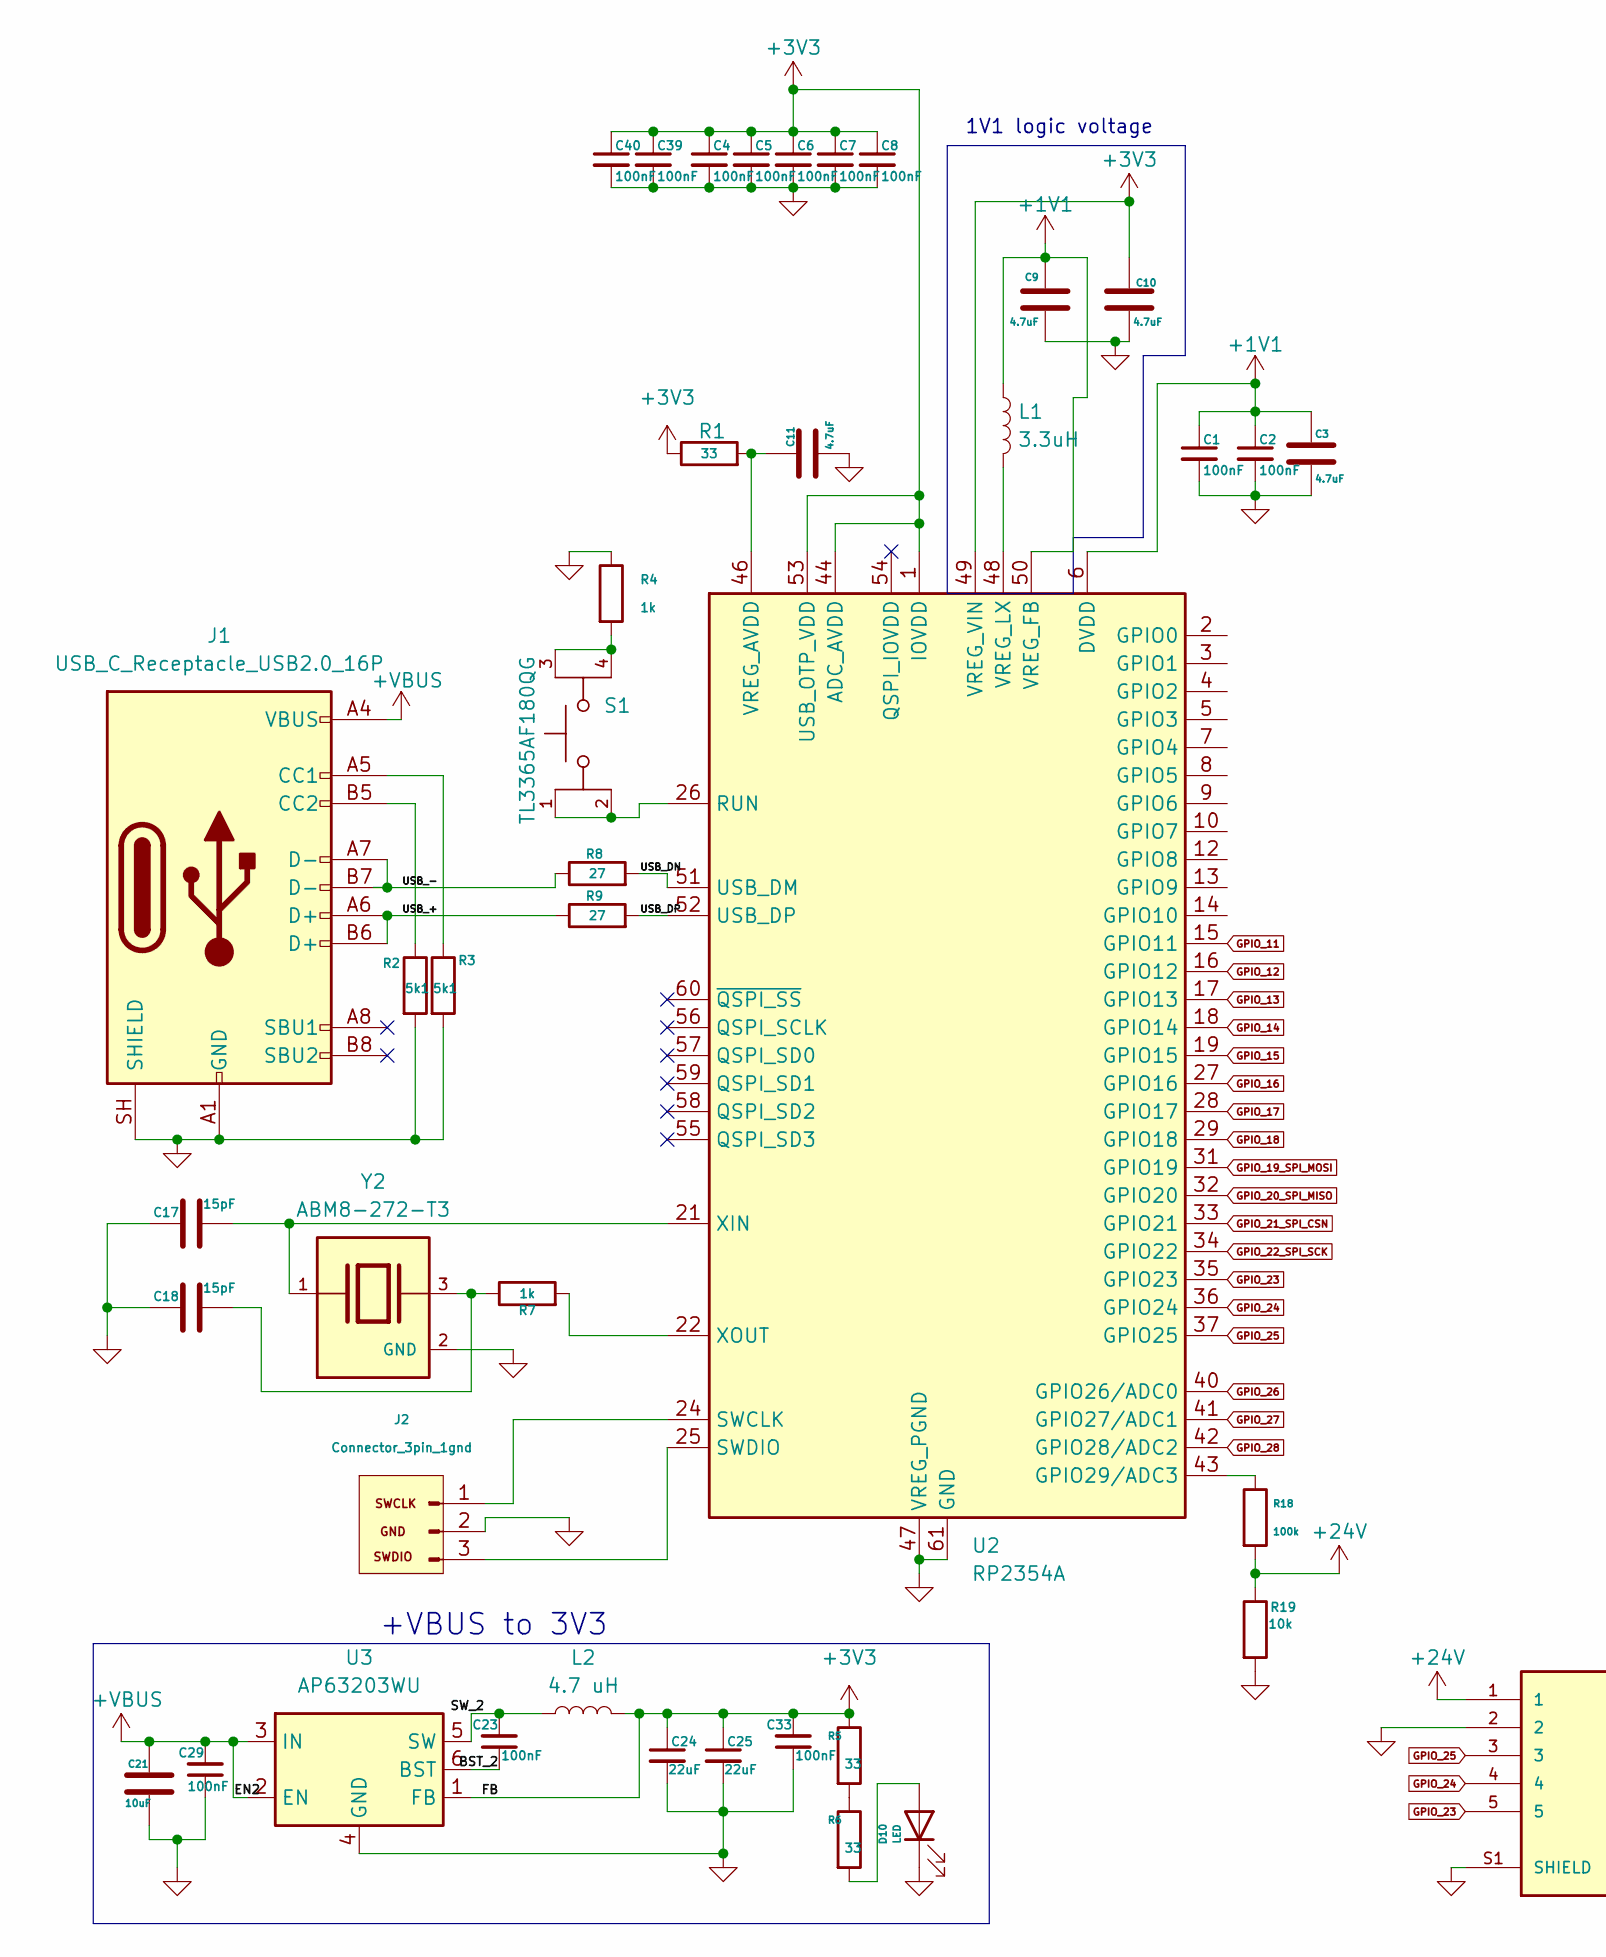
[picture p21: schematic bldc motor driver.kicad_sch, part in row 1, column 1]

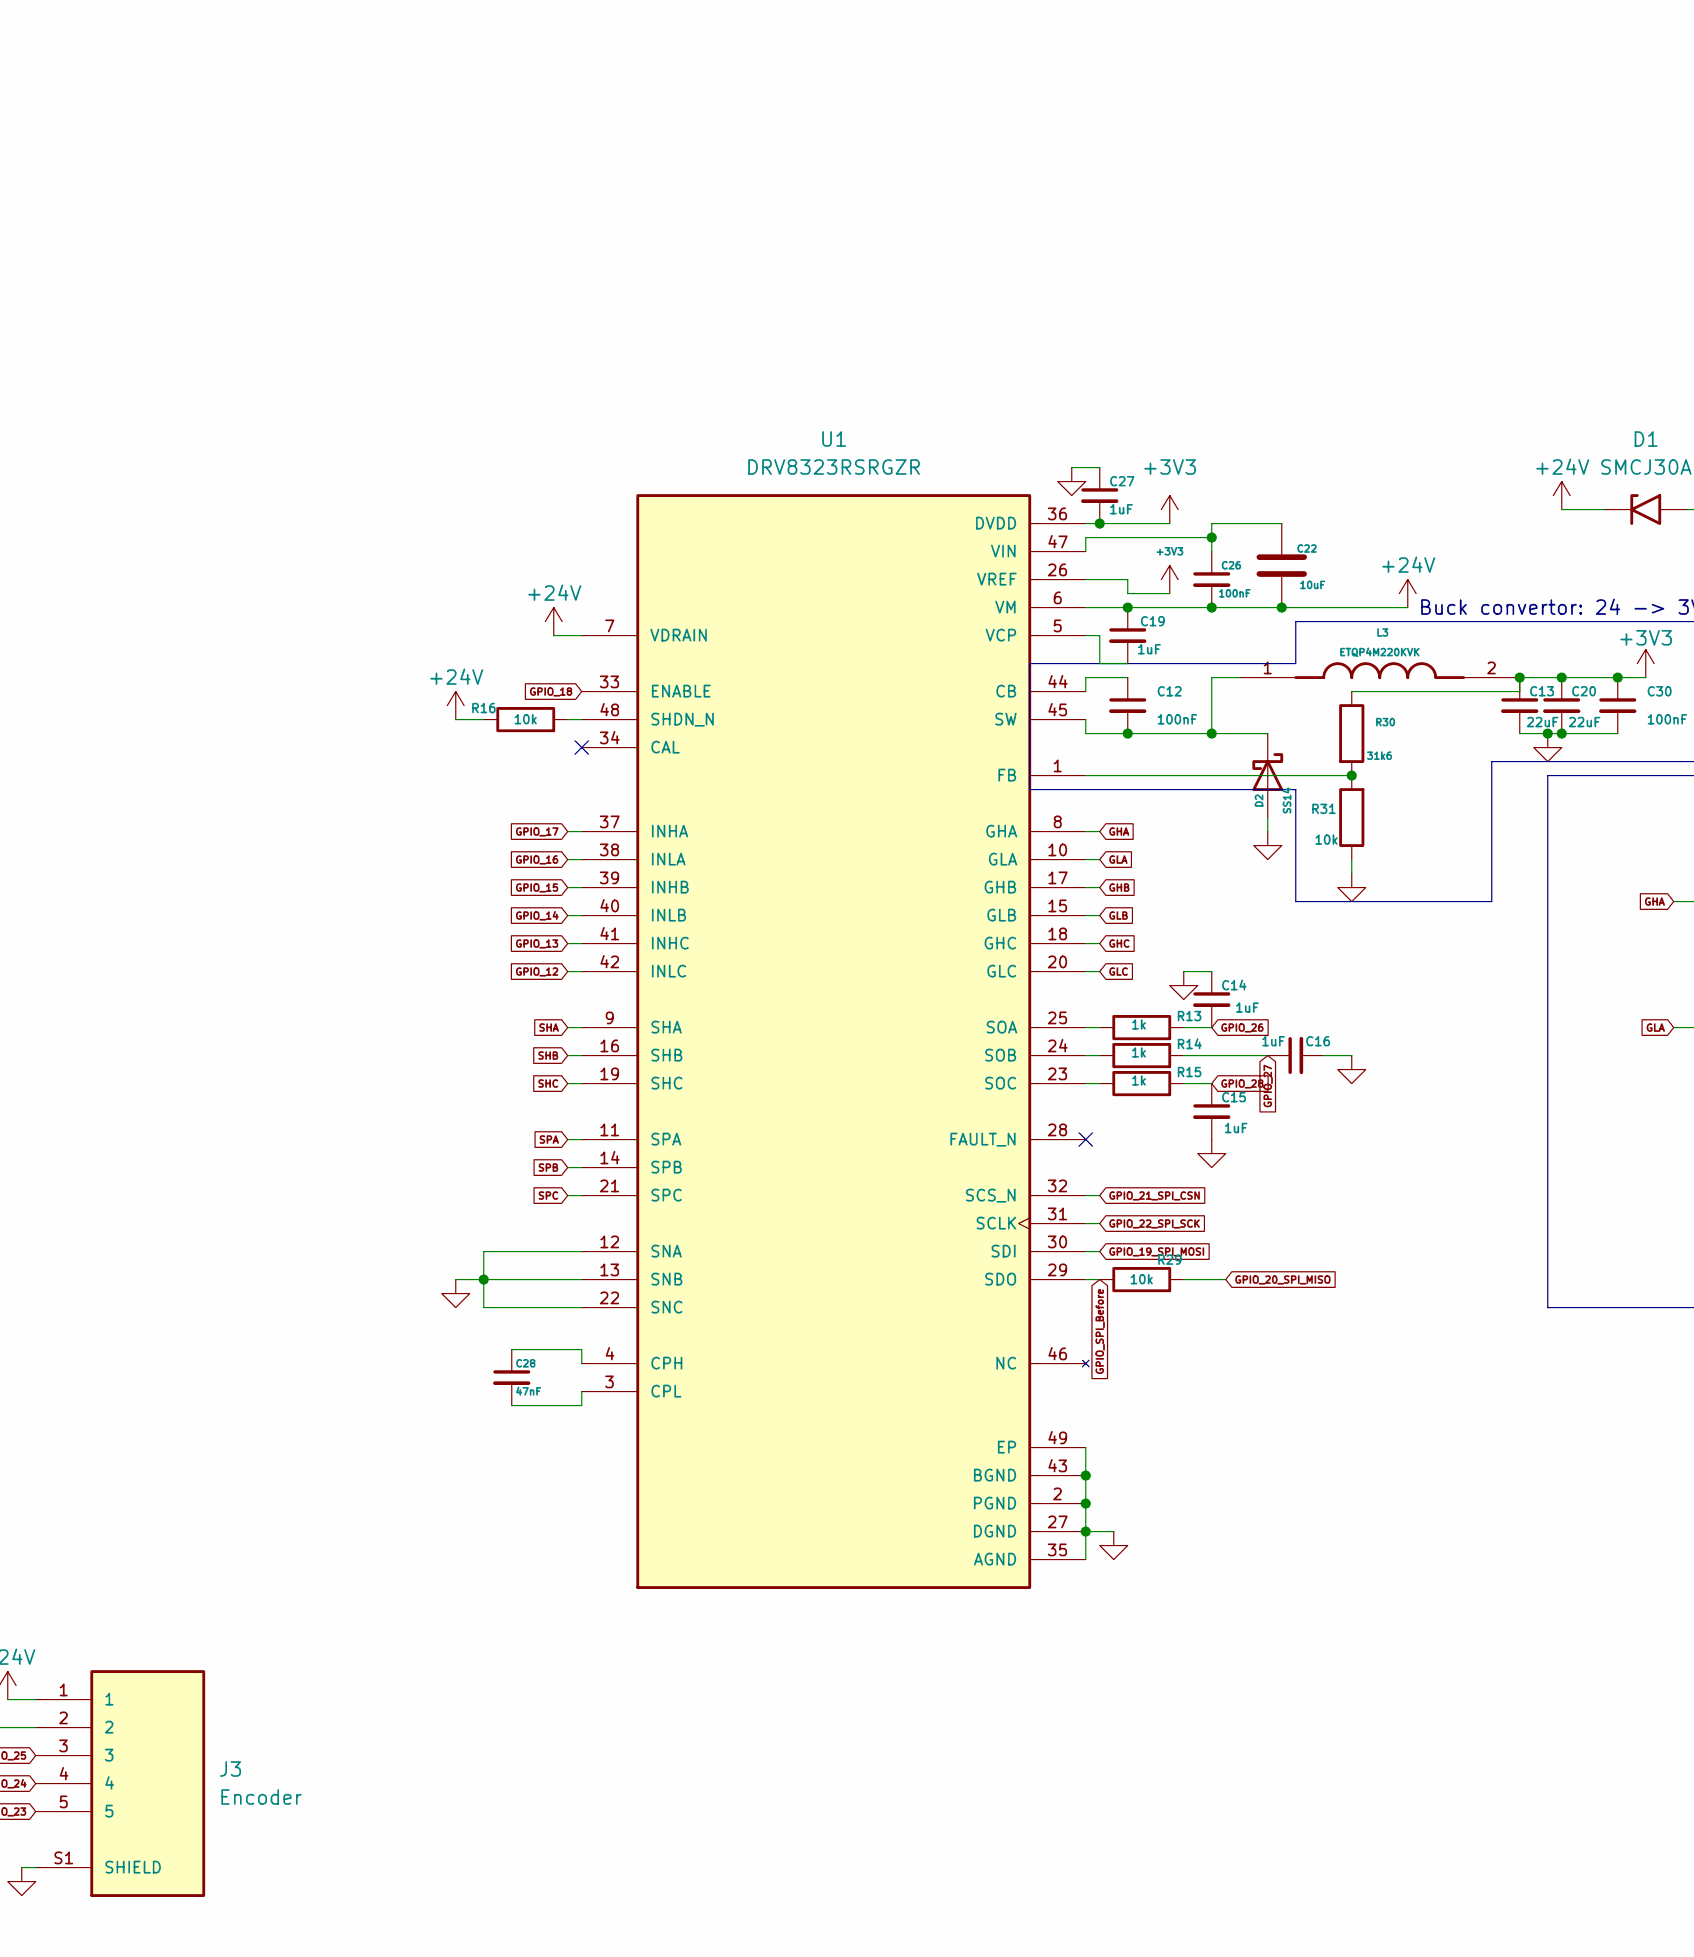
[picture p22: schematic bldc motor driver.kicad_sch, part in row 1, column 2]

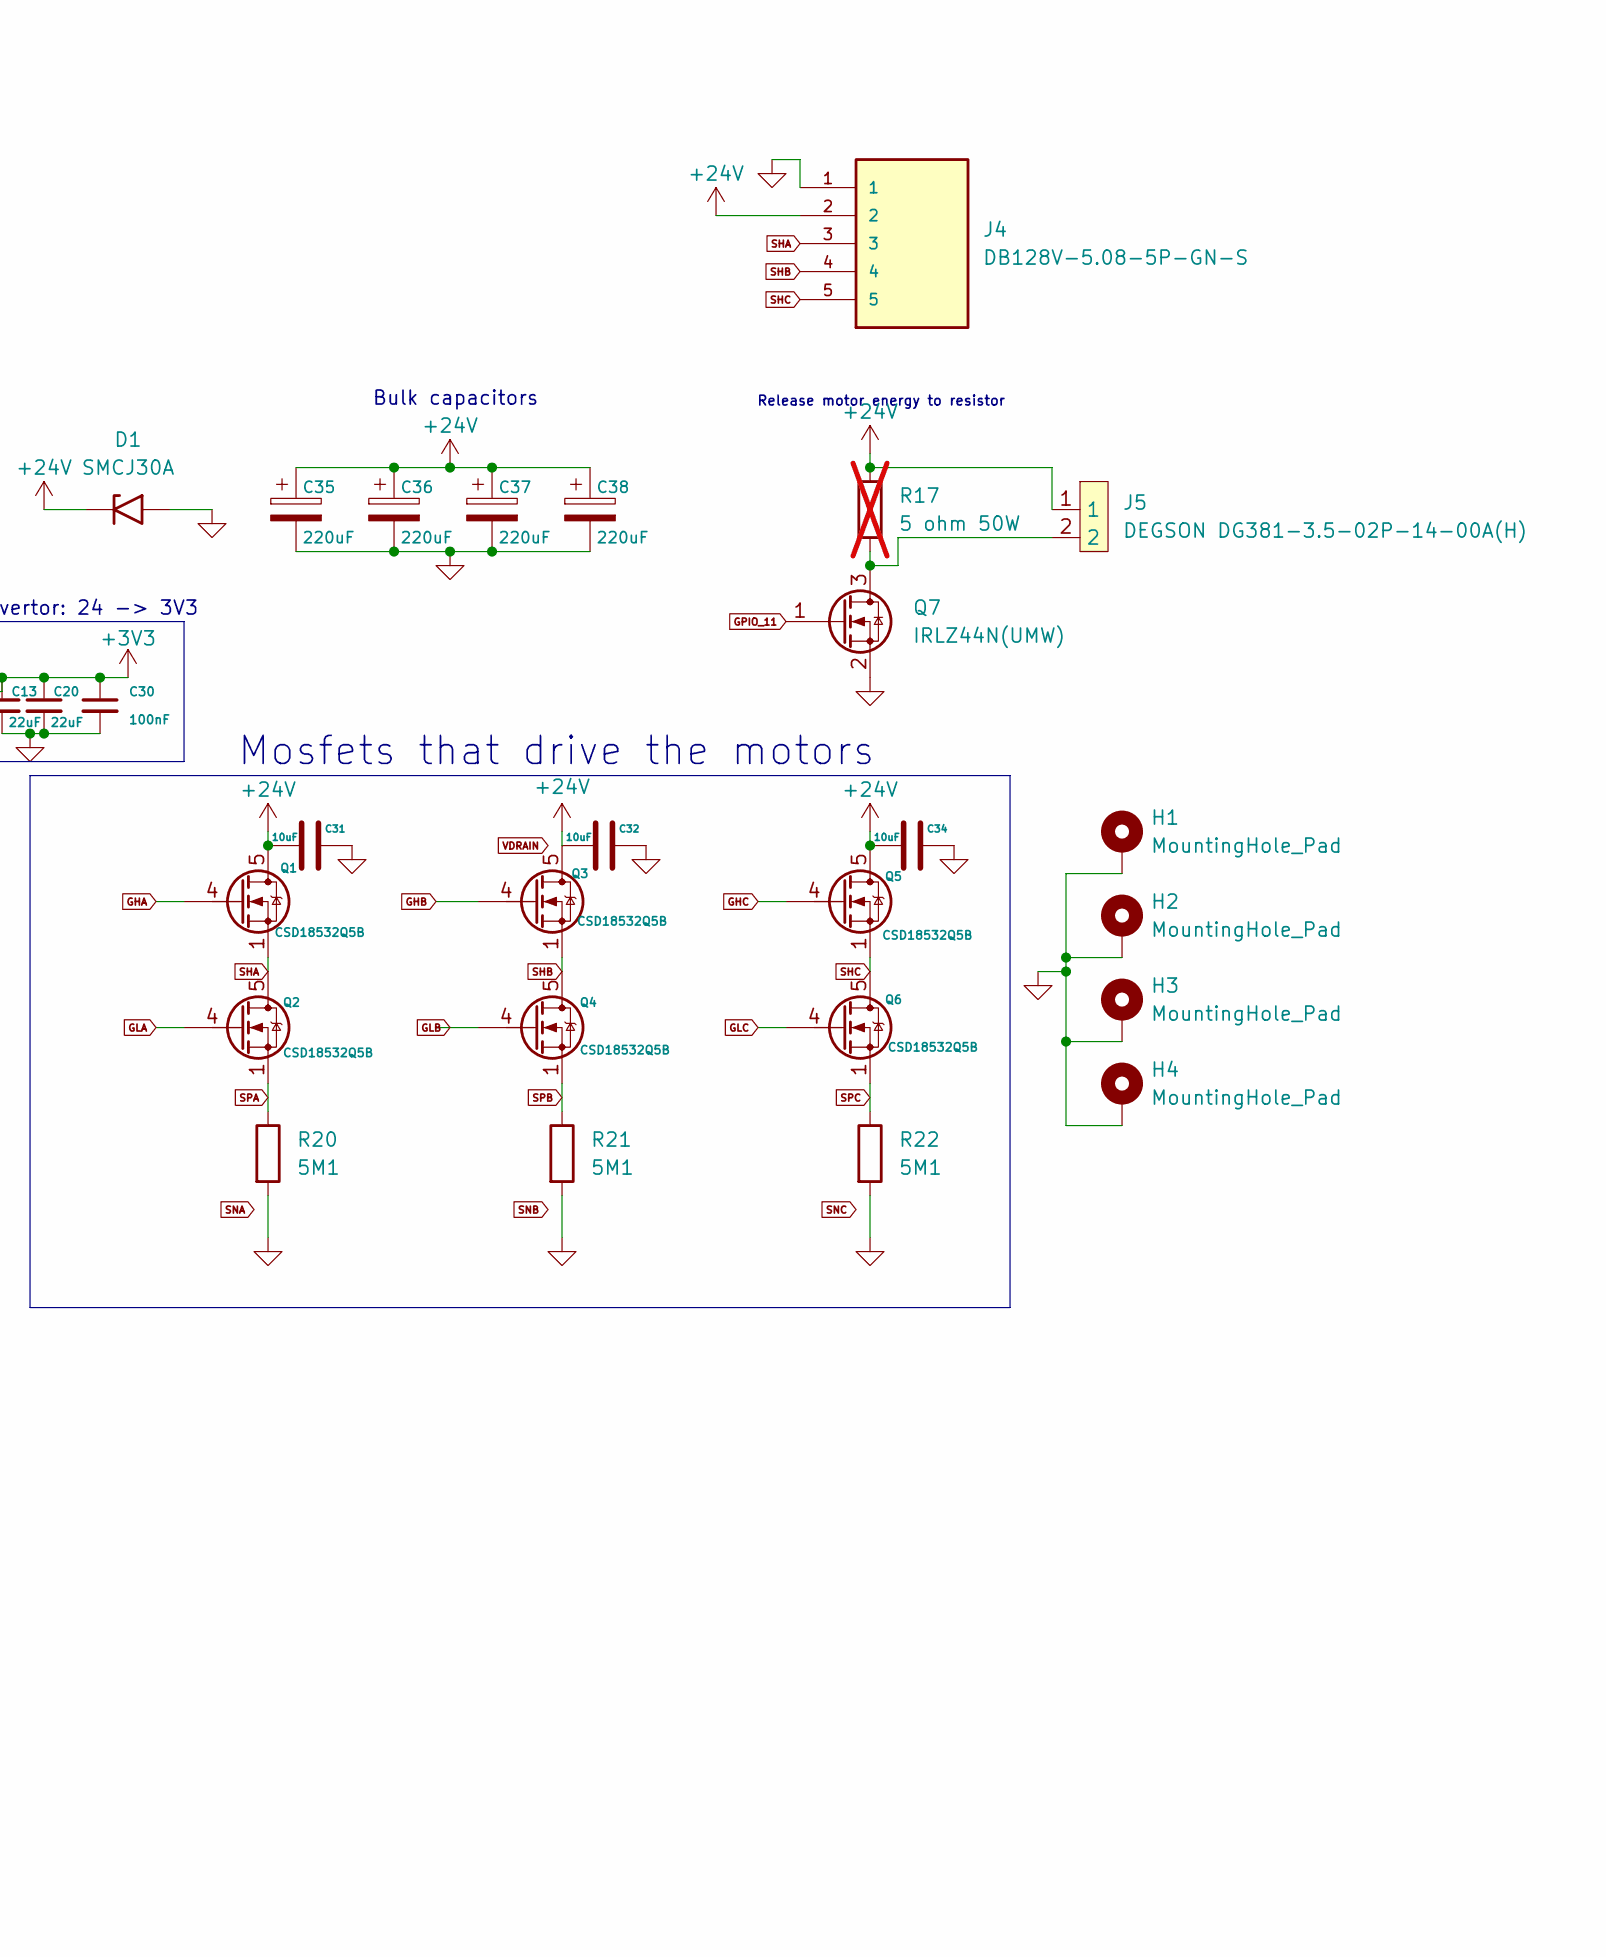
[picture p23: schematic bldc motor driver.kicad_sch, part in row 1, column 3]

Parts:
C1, C2, C4, C5, C6, C7, C8, C12, C30, C39, C40: 100nF; C_0402_1005Metric; MPN CL05B104KO5NNNC; LCSC C1525
C3, C9, C10, C11: 4.7uF; C_0402_1005Metric; MPN CL05A475MP5NRNC; LCSC C23733
C13, C20, C24, C25: 22uF; C_0805_2012Metric; MPN GXT21BR61C226ME13L; LCSC C711104
C14, C15, C16, C19, C27: 1uF; C_0603_1608Metric; MPN CL10A105KB8NNNC; LCSC C15849
C17, C18: 15pF; C_0402_1005Metric smaller silk; MPN GRM1555C1H150FA01D; LCSC C161530
C21, C22, C31, C32, C34: 10uF; C_0805_2012Metric; MPN GRM21BR61H106KE43L; LCSC C440198
C23, C29, C33: 100nF; C_0402_1005Metric smaller silk; MPN CL05B104KO5NNNC; LCSC C1525
C26: 100nF; C_0603_1608Metric; MPN CL10B104KB8NNNC; LCSC C1591
C28: 47nF; C_0603_1608Metric; MPN CL10B473KB8NNNC; LCSC C1622
C35, C36, C37, C38: 220uF; CAP_EEEFK1H221P; MPN RVT1H221M1010; LCSC C72499
D1: SMCJ30A; D_SMC; MPN SMCJ30A; LCSC C4154618
D2: SS14; D_SMA; MPN SS14; LCSC C2837270
D10: LED; LED_0402_1005Metric; MPN SZYY0402G; LCSC C434446
H1, H2, H3, H4: MountingHole_Pad; MountingHole_2.2mm_M2_DIN965_Pad
J1: USB_C_Receptacle_USB2.0_16P; USB_C_Receptacle_G-Switch_GT-USB-7051x
J2: Connector_3pin_1gnd; 3 pin connector middle ground
J3: Encoder; JST_SH_BM05B-SRSS-TB_1x05-1MP_P1.00mm_Vertical; PARTREV N/A
J4: DB128V-5.08-5P-GN-S; DORABO DB128V-5.08-5P-GN-S; MPN DB128V-5.08-5P-GN-S; LCSC C2927513
J5: DEGSON DG381-3.5-02P-14-00A(H); MPN DG381-3.5-02P-14-00A(H); LCSC C5272864
L1: 3.3uH; AOTA-B201610S3R3-101-T; MPN AOTA-B201610S3R3-101-T; LCSC C42411119
L2: 4.7 uH; VLS6045EX-4R7M-H; MPN VLS6045EX-4R7M-H; LCSC C360735
L3: ETQP4M220KVK; IND_ETQP4M220KVK; PARTREV 1-Feb-20; LCSC C542324
Q1, Q2, Q3, Q4, Q5, Q6: CSD18532Q5B; TDSON-8-1
Q7: IRLZ44N(UMW); SOT-23; MPN IRLZ44N(UMW); LCSC C42370423
R1, R5, R6: 33; R_0402_1005Metric; MPN 0402WGF330JTCE; LCSC C25105
R2, R3: 5k1; R_0402_1005Metric smaller silkscreen; MPN 0402WGF5101TCE; LCSC C25905
R4, R13, R14, R15: 1k; R_0402_1005Metric; MPN 0402WGF1001TCE; LCSC C11702
R7: 1k; R_0402_1005Metric smaller silkscreen; MPN 0402WGF1001TCE; LCSC C11702
R8, R9: 27; R_0402_1005Metric; MPN ERJ-2GEJ270X; LCSC C278580
R16, R19, R29, R31: 10k; R_0402_1005Metric smaller silkscreen; MPN 0402WGF1002TCE; LCSC C25744
R17: 5 ohm 50W; MPN HoRX-50W-5R-5%; LCSC C2923747; not fitted
R18: 100k; R_0402_1005Metric; MPN 0402WGF1003TCE; LCSC C25741
R20, R21, R22: 5M1; R_2512_6332Metric; MPN 25121WJ0515T4E; LCSC C419720
R30: 31k6; R_0402_1005Metric; MPN 0402WGF3162TCE; LCSC C11463
S1: TL3365AF180QG; SW_TL3365AF180QG; PARTREV A
U1: DRV8323RSRGZR; QFN-48-1EP_7x7mm_P0.5mm_EP5.3x5.3mm; PARTREV C
U2: RP2354A; QFN-60-1EP_7x7mm_P0.4mm_EP3.4x3.4mm
U3: AP63203WU; TSOT-23-6; MPN AP63203WU-7; LCSC C780769
Y2: ABM8-272-T3; XTAL_ABM8-272-T3; PARTREV 07-29-20; LCSC C20625731

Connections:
+1V1: C1.1, C2.1, C3.1, C9.1, L1.1, U2.6 (DVDD), U2.23 (DVDD), U2.39 (DVDD), U2.50 (VREG_FB)
+3V3: C4.1, C5.1, C6.1, C7.1, C8.1, C10.1, C13.1, C20.1, C24.1, C25.1, C27.2, C30.1, C33.2, C39.1, C40.1, L2.2, L3.2, R1.1, R5.1, R30.1, U1.26 (VREF), U1.36 (DVDD), U2.1 (IOVDD), U2.11 (IOVDD), U2.20 (IOVDD), U2.30 (IOVDD), U2.38 (IOVDD), U2.44 (ADC_AVDD), U2.45 (IOVDD), U2.49 (VREG_VIN), U2.53 (USB_OTP_VDD), U3.1 (FB)
+24V: C19.1, C22.2, C26.2, C31.1, C32.1, C34.1, C35.1, C36.1, C37.1, C38.1, D1.1 (A1), J3.1, J4.2, J5.1, Q1.5 (D), Q3.5 (D), Q5.5 (D), R16.1, R17.1, R18.2, R19.1, U1.6 (VM), U1.7 (VDRAIN); also elsewhere on the board
+VBUS: C21.1, C29.2, J1.A4 (VBUS), J1.A9 (VBUS), J1.B4 (VBUS), J1.B9 (VBUS), U3.2 (EN), U3.3 (IN)
/BST_2: C23.1, U3.6 (BST)
/SW_2: C23.2, L2.1, U3.5 (SW)
/USB_+: J1.A6 (D+), J1.B6 (D+), R9.1
/USB_-: J1.A7 (D-), J1.B7 (D-), R8.1
/USB_DN: R8.2, U2.51 (USB_DM)
/USB_DP: R9.2, U2.52 (USB_DP)
GHA: Q1.4 (G), U1.8 (GHA)
GHB: Q3.4 (G), U1.17 (GHB)
GHC: Q5.4 (G), U1.18 (GHC)
GLA: Q2.4 (G), U1.10 (GLA)
GLB: Q4.4 (G), U1.15 (GLB)
GLC: Q6.4 (G), U1.20 (GLC)
GND: C1.2, C2.2, C3.2, C4.2, C5.2, C6.2, C7.2, C8.2, C9.2, C10.2, C11.2, C13.2, C14.1, C15.2, C16.2, C17.1, C18.1, C20.2, C21.2, C24.2, C25.2, C27.1, C29.1, C30.2, C31.2, C32.2, C33.1, C34.2, C35.2, C36.2, C37.2, C38.2, C39.2, C40.2, D1.2 (A2), D2.2 (A), D10.1 (K), H1.1 (1_1), H2.1 (1_1), H3.1 (1_1), H4.1 (1_1), J1.A1 (GND), J1.A12 (GND), J1.B1 (GND), J1.B12 (GND), J1.SH (SHIELD), J2.2 (GND), J3.2, J3.S1 (SHIELD), J3.S2 (SHIELD), J4.1, Q7.2 (S), R2.2, R3.2, R4.1, R19.2, R20.2, R21.2, R22.2, R31.1, U1.2 (PGND), U1.12 (SNA), U1.13 (SNB), U1.22 (SNC), U1.27 (DGND), U1.35 (AGND), U1.43 (BGND), U1.49 (EP), U2.47 (VREG_PGND), U2.61 (GND), U3.4 (GND), Y2.2 (GND), Y2.4 (GND)
GPIO_11: Q7.1 (G), U2.15 (GPIO11)
GPIO_12: U1.42 (INLC), U2.16 (GPIO12)
GPIO_13: U1.41 (INHC), U2.17 (GPIO13)
GPIO_14: U1.40 (INLB), U2.18 (GPIO14)
GPIO_15: U1.39 (INHB), U2.19 (GPIO15)
GPIO_16: U1.38 (INLA), U2.27 (GPIO16)
GPIO_17: U1.37 (INHA), U2.28 (GPIO17)
GPIO_18: U1.33 (ENABLE), U2.29 (GPIO18)
GPIO_19_SPI_MOSI: U1.30 (SDI), U2.31 (GPIO19)
GPIO_20_SPI_MISO: R29.2, U2.32 (GPIO20)
GPIO_21_SPI_CSN: U1.32 (SCS_N), U2.33 (GPIO21)
GPIO_22_SPI_SCK: U1.31 (SCLK), U2.34 (GPIO22)
GPIO_23: J3.5, U2.35 (GPIO23)
GPIO_24: J3.4, U2.36 (GPIO24)
GPIO_25: J3.3, U2.37 (GPIO25)
GPIO_26: C14.2, R13.2, U2.40 (GPIO26/ADC0)
GPIO_27: C16.1, R14.2, U2.41 (GPIO27/ADC1)
GPIO_28: C15.1, R15.2, U2.42 (GPIO28/ADC2)
GPIO_SPI_Before: R29.1, U1.29 (SDO)
unnamed: C18.2, R7.1, Y2.3
unnamed: C12.2, D2.1 (K), L3.1, U1.45 (SW)
unnamed: D10.2 (A), R6.2
unnamed: J1.A5 (CC1), R3.1
unnamed: J1.B5 (CC2), R2.1
unnamed: J2.1 (SWCLK), U2.24 (SWCLK)
unnamed: J2.3 (SWDIO), U2.25 (SWDIO)
unnamed 43: J5.2, Q7.3 (D), R17.2; also elsewhere on the board
unnamed: R4.2, S1.3, S1.4
unnamed: R5.2, R6.1
unnamed: C12.1, U1.44 (CB)
unnamed: C28.1, U1.4 (CPH)
unnamed: C28.2, U1.3 (CPL)
unnamed: R30.2, R31.2, U1.1 (FB)
unnamed: R16.2, U1.48 (SHDN_N)
unnamed: R13.1, U1.25 (SOA)
unnamed: R14.1, U1.24 (SOB)
unnamed: R15.1, U1.23 (SOC)
unnamed: C19.2, U1.5 (VCP)
unnamed: C22.1, C26.1, U1.47 (VIN)
unnamed: R18.1, U2.43 (GPIO29/ADC3)
unnamed: S1.1, S1.2, U2.26 (RUN)
unnamed: C11.1, R1.2, U2.46 (VREG_AVDD)
unnamed: L1.2, U2.48 (VREG_LX)
unnamed: C17.2, U2.21 (XIN), Y2.1
unnamed: R7.2, U2.22 (XOUT)
SHA: J4.3, Q1.1 (S), Q1.2 (S), Q1.3 (S), Q2.5 (D), U1.9 (SHA)
SHB: J4.4, Q3.1 (S), Q3.2 (S), Q3.3 (S), Q4.5 (D), U1.16 (SHB)
SHC: J4.5, Q5.1 (S), Q5.2 (S), Q5.3 (S), Q6.5 (D), U1.19 (SHC)
SPA: Q2.1 (S), Q2.2 (S), Q2.3 (S), R20.1, U1.11 (SPA)
SPB: Q4.1 (S), Q4.2 (S), Q4.3 (S), R21.1, U1.14 (SPB)
SPC: Q6.1 (S), Q6.2 (S), Q6.3 (S), R22.1, U1.21 (SPC)

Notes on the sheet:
Bulk capacitors
+VBUS to 3V3
Release motor energy to resistor
Mosfets that drive the motors
Buck convertor: 24 -> 3V3
1V1 logic voltage

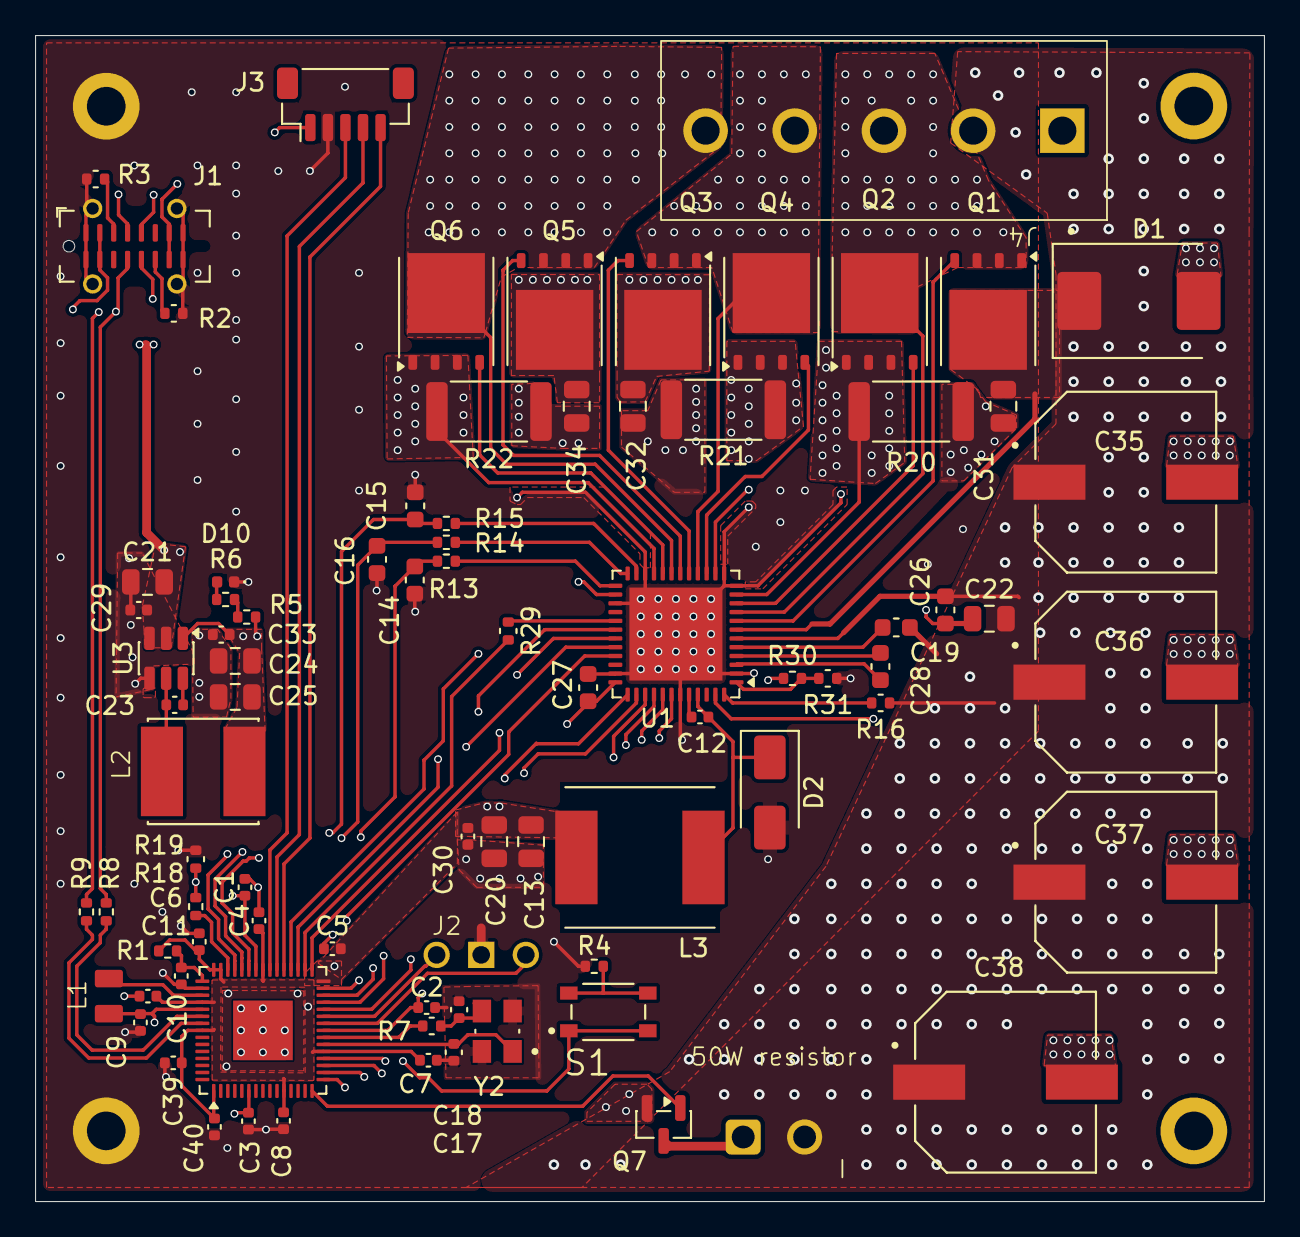
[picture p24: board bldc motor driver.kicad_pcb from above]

Board: 4 copper layers, 70.0 x 66.4 mm, 88 parts (0 on the bottom side), 68 nets.

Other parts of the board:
50W resistor: DEGSON DG381-3.5-02P-14-00A(H)

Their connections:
+24V: 50W resistor.1; also elsewhere on the board
unnamed 43: 50W resistor.2; also elsewhere on the board

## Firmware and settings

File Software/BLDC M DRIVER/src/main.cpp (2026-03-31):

#include <stdio.h>
#include <stdlib.h>
#include "pico/stdlib.h"
#include "pico/multicore.h"
#include "pico/time.h"
#include "hardware/irq.h"
#include "hardware/timer.h"
#include "hardware/gpio.h"
#include "hardware/adc.h"

#include "config.h"
#include "encoder_driver.h"
#include "current_sense.h"
#include "foc_controller.h"
#include "motor_control.h"
#include "drv8323_driver.h"
#include "usb_hid_device.h"

// Synchronization flags and shared data
volatile float g_target_iq = 0.0f;  // Target current from USB HID
volatile float g_wheel_position = 0.0f;  // Current wheel position
volatile float g_wheel_velocity = 0.0f;  // Current wheel angular velocity
volatile uint32_t g_fault_flags = 0;  // System fault flags

#define FAULT_FLAG_OVERCURRENT (1 << 0)
#define FAULT_FLAG_OVERVOLTAGE (1 << 1)
#define FAULT_FLAG_DRV_FAULT (1 << 2)
#define FAULT_FLAG_USB_TIMEOUT (1 << 3)

// Watchdog timeout for USB communication (Core 0 should update this regularly)
static uint32_t usb_last_update_time = 0;
static uint32_t foc_loop_count = 0;

// Voltage monitoring
static void voltage_monitor_init(void) {
    gpio_init(GPIO_MOSFET_EN);
    gpio_set_dir(GPIO_MOSFET_EN, GPIO_OUT);
    gpio_put(GPIO_MOSFET_EN, 0);  // Dissipation resistor off by default
}

static float voltage_monitor_read(void) {
    adc_select_input(3);  // GPIO 29 is ADC input 3
    uint16_t adc_value = adc_read();
    
    // Convert ADC to voltage
    float v_adc = (adc_value / 4096.0f) * 3.3f;
    
    // Account for divider (10x divider from 24V line)
    float v_battery = v_adc * VBATT_DIVIDER_RATIO;
    
    return v_battery;
}

static void voltage_monitor_check(void) {
    static uint32_t monitor_timer = 0;
    
    // Check voltage periodically (every 100ms)
    uint32_t now_us = time_us_32();
    if ((now_us - monitor_timer) < 100000) return;
    monitor_timer = now_us;
    
    float v_batt = voltage_monitor_read();
    
    if (v_batt > VBATT_OVERVOLT_THRESH) {
        // Overvoltage detected - activate dissipation resistor
        gpio_put(GPIO_MOSFET_EN, 1);
        g_fault_flags |= FAULT_FLAG_OVERVOLTAGE;
    } else if (v_batt < VBATT_OVERVOLT_THRESH - 1.0f) {
        // Overvoltage cleared
        gpio_put(GPIO_MOSFET_EN, 0);
        g_fault_flags &= ~FAULT_FLAG_OVERVOLTAGE;
    }
}

// ============================================================================
// CORE 1 - High-speed FOC Control Loop (20kHz)
// ============================================================================
static void core1_main(void) {
    printf("[Core 1] Initializing motor control...\n");
    
    // Initialize all hardware drivers
    motor_control_init();
    drv8323_init();
    current_sense_init();
    encoder_init();
    foc_init();
    voltage_monitor_init();
    
    printf("[Core 1] Hardware initialized. Starting FOC loop...\n");
    
    // Start the FOC timer (20kHz)
    uint32_t loop_period_us = 1000000 / FOC_LOOP_FREQ;  // 50µs for 20kHz
    uint32_t last_update_us = time_us_32();
    
    float prev_position = 0.0f;
    uint32_t prev_time_us = time_us_32();
    
    while (1) {
        uint32_t now_us = time_us_32();
        uint32_t elapsed_us = now_us - prev_time_us;
        
        // Check if it's time for the next FOC update (every ~50µs)
        if (elapsed_us < loop_period_us) {
            continue;  // Wait for next cycle
        }
        
        float dt_seconds = elapsed_us / 1e6f;
        prev_time_us = now_us;
        
        // ---- FOC Control Loop (runs at 20kHz) ----
        
        // 1. Read encoder position and velocity
        encoder_update();
        encoder_state_t enc = encoder_get_state();
        
        // Calculate velocity (rad/s)
        float position_delta = enc.mechanical_angle_rad - prev_position;
        if (position_delta > M_PI) position_delta -= 2.0f * M_PI;
        if (position_delta < -M_PI) position_delta += 2.0f * M_PI;
        g_wheel_velocity = position_delta / dt_seconds;
        prev_position = enc.mechanical_angle_rad;
        
        g_wheel_position = enc.electrical_angle_rad;
        
        // 2. Read phase currents (must sync with PWM)
        current_sense_update();
        current_sense_state_t curr = current_sense_get_state();
        
        // Check over-current fault
        if (curr.over_current) {
            g_fault_flags |= FAULT_FLAG_OVERCURRENT;
            motor_control_stop();
        } else {
            g_fault_flags &= ~FAULT_FLAG_OVERCURRENT;
        }
        
        // 3. Run FOC controller (Clarke + Park + PI + InvPark + SVPWM)
        if (!(g_fault_flags & (FAULT_FLAG_OVERCURRENT | FAULT_FLAG_OVERVOLTAGE))) {
            foc_update(enc.electrical_angle_rad, curr.i_alpha, curr.i_beta, dt_seconds);
            foc_state_t foc = foc_get_state();
            
            // Get SVPWM duty cycles
            float duty_a, duty_b, duty_c;
            svpwm(foc.vout_alpha, foc.vout_beta, &duty_a, &duty_b, &duty_c);
            
            // Apply to motor
            motor_control_set_duty(duty_a, duty_b, duty_c);
        }
        
        // 4. Check DRV8323 faults
        drv8323_fault_t drv_fault = drv8323_get_fault_status();
        if (drv_fault.fault) {
            g_fault_flags |= FAULT_FLAG_DRV_FAULT;
            motor_control_stop();
        }
        
        // 5. Voltage monitoring
        voltage_monitor_check();
        
        foc_loop_count++;
    }
}

// ============================================================================
// CORE 0 - USB HID Communication & Logic (1kHz)
// ============================================================================
int main(void) {
    stdio_init_all();
    
    printf("\n=== BLDC Motor Driver with FOC - RP2354 ===\n");
    printf("Assetto Corsa Force Feedback Wheel\n\n");
    
    // Initialize ADC for voltage monitoring on both cores
    adc_init();
    adc_gpio_init(GPIO_VIN_MON);
    
    // Launch Core 1 with the high-speed FOC loop
    printf("[Core 0] Launching Core 1 (FOC control)...\n");
    multicore_launch_core1(core1_main);
    
    // Initialize USB HID device
    printf("[Core 0] Initializing USB HID device...\n");
    usb_hid_init();
    
    sleep_ms(200);  // Wait for Core 1 to initialize
    
    printf("[Core 0] System ready! Waiting for USB connection...\n");
    printf("[Core 0] Connect to Assetto Corsa to begin\n\n");
    
    // Core 0 main loop (1kHz USB communication)
    uint32_t loop_counter = 0;
    uint32_t last_status_print_ms = 0;
    usb_last_update_time = to_ms_since_boot(get_absolute_time());
    
    while (1) {
        // Process USB HID communication
        usb_hid_process();
        usb_last_update_time = to_ms_since_boot(get_absolute_time());
        
        // Check USB connection status
        if (!usb_hid_is_connected()) {
            // USB disconnected - zero out commands for safety
            g_target_iq = 0.0f;
            foc_set_iq_target(0.0f);
        } else {
            // Calculate torque command from USB effects
            float iq_cmd = usb_hid_calculate_torque_command(g_wheel_position, g_wheel_velocity);
            g_target_iq = iq_cmd;
            foc_set_iq_target(iq_cmd);
        }
        
        // Send status back to host
        uint16_t status_flags = (g_fault_flags & 0xFF);
        usb_hid_send_status(g_wheel_position, status_flags);
        
        // Print status periodically (every 500ms)
        absolute_time_t now = get_absolute_time();
        uint32_t now_ms = to_ms_since_boot(now);
        if ((now_ms - last_status_print_ms) >= 500) {
            last_status_print_ms = now_ms;
            
            encoder_state_t enc = encoder_get_state();
            current_sense_state_t curr = current_sense_get_state();
            foc_state_t foc = foc_get_state();
            
            printf("[%05ld] ", foc_loop_count / 20000);  // FOC cycles / frequency
            printf("Pos: %6.1f° | Vel: %7.1f°/s | ", 
                   (enc.mechanical_angle_rad * 180.0f / M_PI),
                   (g_wheel_velocity * 180.0f / M_PI));
            printf("Iq: %6.2f/%6.2f A | ", foc.iq_measured, foc.iq_target);
            printf("USB: %s | ", usb_hid_is_connected() ? "CONN" : "DISC");
            printf("Fault: 0x%02X\n", status_flags);
            
            // Read and print battery voltage
            float v_batt = voltage_monitor_read();
            printf("       Vbatt: %.1fV | Ia: %6.1f A | Ib: %6.1f A | Ic: %6.1f A\n",
                   v_batt, curr.ia_amps, curr.ib_amps, curr.ic_amps);
        }
        
        // Check watchdog timeout
        uint32_t time_since_usb = now_ms - usb_last_update_time;
        if (time_since_usb > WATCHDOG_TIMEOUT_MS) {
            g_fault_flags |= FAULT_FLAG_USB_TIMEOUT;
            foc_set_iq_target(0.0f);  // Safety: zero torque on timeout
        }
        
        // Sleep for ~1ms (1kHz loop)
        sleep_ms(1);
        loop_counter++;
    }
    
    return 0;
}

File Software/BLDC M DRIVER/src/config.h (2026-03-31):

#ifndef CONFIG_H
#define CONFIG_H

#include <stdint.h>

// ============ GPIO PIN DEFINITIONS ============
// Motor Phase Control (PWM outputs to DRV8323)
#define GPIO_INLA 16    // Phase A Low-side
#define GPIO_INHA 17    // Phase A High-side
#define GPIO_INLB 14    // Phase B Low-side
#define GPIO_INHB 15    // Phase B High-side
#define GPIO_INLC 12    // Phase C Low-side
#define GPIO_INHC 13    // Phase C High-side

// DRV8323 SPI Interface
#define GPIO_MOSI 19
#define GPIO_MISO 20
#define GPIO_CSN  21
#define GPIO_SCK  22

// Encoder Inputs (Quadrature)
#define GPIO_ENC_A 23
#define GPIO_ENC_B 24
#define GPIO_ENC_Z 25   // Index pulse (optional calibration)

// Current Sense Inputs (to DRV8323 SOA, SOB, SOC)
#define GPIO_CUR_A 26
#define GPIO_CUR_B 27
#define GPIO_CUR_C 28

// Overvoltage & Power Management
#define GPIO_VIN_MON   29   // Voltage monitor (24V / 10 = 2.4V at ADC)
#define GPIO_MOSFET_EN 11   // Enable dissipation resistor when overvoltage detected

// DRV8323 Control
#define GPIO_DRV_EN 18      // Enable (set high always)
#define GPIO_DRV_FAULT 10   // Fault input (optional, for safety)

// ============ SYSTEM CONFIGURATION ============
#define PWM_FREQUENCY 20000 // 20kHz PWM frequency
#define FOC_LOOP_FREQ 20000 // 20kHz FOC control loop
#define USB_POLL_FREQ 1000  // 1kHz USB polling on Core 0

// ============ MOTOR & ELECTRICAL PARAMETERS ============
#define MOTOR_POLE_PAIRS 15         // Hoverboard motor typically has 15-20 pole pairs
#define MOTOR_MAX_DEGREES 900       // ±450° rotation (typical racing wheel)
#define ENCODER_CPR 3000            // Counts per revolution (depends on physical encoder)
#define ENCODER_ELECTRICAL_OFFSET_POS_OFFSET 0  // Calibrated at startup with Z-index

// ============ CONTROL LOOP PARAMETERS ============
#define IQ_PID_KP 0.5f      // Proportional gain for current loop
#define IQ_PID_KI 0.1f      // Integral gain
#define IQ_PID_KD 0.01f     // Derivative gain

#define POSITION_PID_KP 0.3f  // For position tracking (if used)
#define POSITION_PID_KI 0.05f
#define POSITION_PID_KD 0.02f

#define TORQUE_SLEW_RATE 50.0f  // Limit rapid torque changes (A/ms) for safety

// ============ CURRENT SENSE PARAMETERS ============
#define DRV8323_SHUNT_RESISTOR 0.01f  // 10mΩ shunt resistor (ohms)
#define DRV8323_GAIN 20.0f             // Internal amplifier gain (typical)
#define ADC_VREF 3.3f                  // ADC reference voltage
#define ADC_RESOLUTION 4096.0f         // 12-bit ADC = 4096 levels

#define CURRENT_SENSE_MAX_MA 40000     // 40A max (in mA)
#define CURRENT_SENSE_WARN_MA 30000    // 30A warning threshold
#define CURRENT_SENSE_CUTOFF_MA 35000  // 35A hard cutoff

// ============ VOLTAGE MONITORING ============
#define VBATT_NOMINAL 24.0f         // Nominal battery voltage
#define VBATT_OVERVOLT_THRESH 25.0f // Overvoltage threshold for dissipation resistor
#define VBATT_DIVIDER_RATIO 10.0f    // 24V / 10 = 2.4V at ADC pin
#define VBATT_ADC_PIN 29

// ============ USB HID PARAMETERS ============
#define USB_VENDOR_ID 0x1234
#define USB_PRODUCT_ID 0x5678
#define USB_MANUFACTURER "DIY"
#define USB_PRODUCT "Direct Drive Wheel"
#define USB_SERIAL "DD-WHEEL-001"

// ============ EFFECT PARAMETERS ============
#define MAX_EFFECTS 4  // Number of simultaneous effects supported
#define EFFECT_CONSTANT_FORCE 0x01
#define EFFECT_SPRING 0x02
#define EFFECT_DAMPER 0x03
#define EFFECT_FRICTION 0x04

// ============ SAFETY LIMITS ============
#define WATCHDOG_TIMEOUT_MS 1000  // 1 second watchdog for USB communication
#define CALIBRATION_TIMEOUT_MS 5000 // 5 seconds for startup calibration

#endif // CONFIG_H

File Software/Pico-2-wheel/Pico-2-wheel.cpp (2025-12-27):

#include <stdio.h>
#include "pico/stdlib.h"
#include "pico/multicore.h"
#include "hardware/spi.h"


struct InputPayload {
    uint32_t buttons;
    int32_t encoder_diff[6];
};

struct EncoderMap {
    uint8_t pinA; 
    uint8_t pinB;
};

// 2. CONFIGURATION
#define ROWS 5
#define COLS 6
#define NUM_ENCODERS 6 
#define DEBOUNCE_THRESHOLD 5 

const uint row_pins[ROWS] = {2, 3, 4, 5, 6};
const uint col_pins[COLS] = {7, 8, 9, 10, 11, 12};

#define SPI_PORT spi0
#define PIN_MISO 16 
#define PIN_CS   17 
#define PIN_SCK  18 
#define PIN_MOSI 19 


EncoderMap encoders[NUM_ENCODERS] = {
    {0, 1},   
    {2, 3},   
    {4, 5},   
    {6, 7},   
    {8, 9},   
    {10, 11} 
};


void core1_entry() {
    for (int i = 0; i < ROWS; i++) {
        gpio_init(row_pins[i]);
        gpio_set_dir(row_pins[i], GPIO_IN);
        gpio_pull_down(row_pins[i]);
    }
    for (int i = 0; i < COLS; i++) {
        gpio_init(col_pins[i]);
        gpio_set_dir(col_pins[i], GPIO_OUT);
        gpio_put(col_pins[i], 0);
    }

    while (1) {
        uint32_t scan = 0;
        for (int c = 0; c < COLS; c++) {
            gpio_put(col_pins[c], 1);
            sleep_us(2); 
            for (int r = 0; r < ROWS; r++) {
                if (gpio_get(row_pins[r])) {
                    scan |= (1 << (c * ROWS + r));
                }
            }
            gpio_put(col_pins[c], 0);
        }
        multicore_fifo_push_blocking(scan);
    }
}

int main() {
    stdio_init_all();

    spi_init(SPI_PORT, 1000 * 1000); 
    spi_set_slave(SPI_PORT, true);
    gpio_set_function(PIN_MISO, GPIO_FUNC_SPI);
    gpio_set_function(PIN_SCK, GPIO_FUNC_SPI);
    gpio_set_function(PIN_MOSI, GPIO_FUNC_SPI);
    gpio_set_function(PIN_CS, GPIO_FUNC_SPI);

    multicore_launch_core1(core1_entry);

    uint8_t debounce_counters[30] = {0};
    uint8_t encoder_states[6] = {0}; 
    const int8_t encoder_table[] = {0,1,-1,0,-1,0,0,1,1,0,0,-1,0,-1,1,0};
    
    InputPayload payload = {0};

    while (1) {
        if (multicore_fifo_rvalid()) {
            uint32_t raw_bits = multicore_fifo_pop_blocking();

            uint32_t current_debounced_state = 0;
            for (int i = 0; i < 30; i++) {
                bool is_high = (raw_bits >> i) & 1;
                if (is_high) {
                    if (debounce_counters[i] < DEBOUNCE_THRESHOLD) debounce_counters[i]++;
                } else {
                    if (debounce_counters[i] > 0) debounce_counters[i]--;
                }
                if (debounce_counters[i] == DEBOUNCE_THRESHOLD) current_debounced_state |= (1 << i);
            }

            for (int e = 0; e < NUM_ENCODERS; e++) {
                uint8_t a = (current_debounced_state >> encoders[e].pinA) & 1;
                uint8_t b = (current_debounced_state >> encoders[e].pinB) & 1;
                uint8_t state = (encoder_states[e] << 2) | (a << 1) | b;
                payload.encoder_diff[e] += encoder_table[state & 0x0F];
                encoder_states[e] = (a << 1) | b;
            }
            payload.buttons = current_debounced_state;


            spi_write_read_blocking(SPI_PORT, (uint8_t*)&payload, NULL, sizeof(payload));

            for(int i=0; i<6; i++) payload.encoder_diff[i] = 0;
        }
    }
}

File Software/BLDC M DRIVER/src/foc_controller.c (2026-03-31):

#include "foc_controller.h"
#include "config.h"
#include <math.h>
#include <string.h>

static foc_state_t foc_state = {0};
static pid_controller_t iq_pid = {0};
static pid_controller_t id_pid = {0};

#define SQRT3 1.732050808f
#define TWO_OVER_SQRT3 1.154700538f

void foc_init(void) {
    memset(&foc_state, 0, sizeof(foc_state));
    
    // Initialize Iq PID controller (current loop)
    pid_init(&iq_pid, IQ_PID_KP, IQ_PID_KI, IQ_PID_KD);
    
    // Initialize Id PID controller (typically set to 0 for max torque)
    pid_init(&id_pid, 0.5f, 0.1f, 0.01f);
    
    foc_state.id_target = 0.0f;    // No field weakening, keep Id = 0
    foc_state.iq_target = 0.0f;
}

void park_transform(float i_alpha, float i_beta, float theta, float *id, float *iq) {
    // Park Transform: converts αβ frame to dq frame (rotor-aligned)
    // d-axis: aligned with rotor flux
    // q-axis: perpendicular to d-axis (torque-producing current)
    //
    // Park equations:
    // id = i_alpha * cos(theta) + i_beta * sin(theta)
    // iq = -i_alpha * sin(theta) + i_beta * cos(theta)
    
    float cos_theta = cosf(theta);
    float sin_theta = sinf(theta);
    
    *id = i_alpha * cos_theta + i_beta * sin_theta;
    *iq = -i_alpha * sin_theta + i_beta * cos_theta;
}

void inv_park_transform(float vd, float vq, float theta, float *v_alpha, float *v_beta) {
    // Inverse Park Transform: converts dq frame back to αβ frame
    //
    // Inverse Park equations:
    // v_alpha = vd * cos(theta) - vq * sin(theta)
    // v_beta = vd * sin(theta) + vq * cos(theta)
    
    float cos_theta = cosf(theta);
    float sin_theta = sinf(theta);
    
    *v_alpha = vd * cos_theta - vq * sin_theta;
    *v_beta = vd * sin_theta + vq * cos_theta;
}

void svpwm(float v_alpha, float v_beta, float *duty_a, float *duty_b, float *duty_c) {
    // Space Vector PWM (SVPWM) modulator
    // Converts 2-phase (alpha-beta) voltage to 3-phase PWM duty cycles
    // This is the standard 60-degree sector method
    
    // Step 1: Calculate sector and time durations
    // Project αβ voltage to 3-phase reference
    float v_a = v_alpha;
    float v_b = -0.5f * v_alpha + (SQRT3 / 2.0f) * v_beta;
    float v_c = -0.5f * v_alpha - (SQRT3 / 2.0f) * v_beta;
    
    // Step 2: Normalize voltage (max = 1.0 represents DC-link voltage)
    float v_ref_mag = sqrtf(v_alpha * v_alpha + v_beta * v_beta);
    if (v_ref_mag > 1.0f) {
        v_a /= v_ref_mag;
        v_b /= v_ref_mag;
        v_c /= v_ref_mag;
    }
    
    // Step 3: Convert to duty cycles (map from [-Vdc/2, Vdc/2] to [0, 1])
    // Add 0.5 offset to shift from [-0.5, 0.5] range to [0, 1] range
    *duty_a = 0.5f + v_a * 0.5f;
    *duty_b = 0.5f + v_b * 0.5f;
    *duty_c = 0.5f + v_c * 0.5f;
    
    // Clamp to [0, 1]
    if (*duty_a > 1.0f) *duty_a = 1.0f;
    if (*duty_a < 0.0f) *duty_a = 0.0f;
    if (*duty_b > 1.0f) *duty_b = 1.0f;
    if (*duty_b < 0.0f) *duty_b = 0.0f;
    if (*duty_c > 1.0f) *duty_c = 1.0f;
    if (*duty_c < 0.0f) *duty_c = 0.0f;
}

void pid_init(pid_controller_t *pid, float kp, float ki, float kd) {
    pid->kp = kp;
    pid->ki = ki;
    pid->kd = kd;
    pid->integral = 0.0f;
    pid->prev_error = 0.0f;
    pid->output = 0.0f;
}

float pid_update(pid_controller_t *pid, float error, float dt) {
    // Proportional term
    float p_term = pid->kp * error;
    
    // Integral term
    pid->integral += pid->ki * error * dt;
    // Anti-windup: limit integral term
    if (pid->integral > 10.0f) pid->integral = 10.0f;
    if (pid->integral < -10.0f) pid->integral = -10.0f;
    
    // Derivative term
    float d_term = 0.0f;
    if (dt > 0.0f) {
        d_term = pid->kd * (error - pid->prev_error) / dt;
    }
    pid->prev_error = error;
    
    // Total output
    pid->output = p_term + pid->integral + d_term;
    
    return pid->output;
}

void pid_reset(pid_controller_t *pid) {
    pid->integral = 0.0f;
    pid->prev_error = 0.0f;
    pid->output = 0.0f;
}

void foc_update(float theta_elec, float i_alpha, float i_beta, float dt_seconds) {
    // Store electrical angle
    foc_state.theta_elec = theta_elec;
    
    // Step 1: Clarke Transform (already done externally, but we need alpha-beta)
    // Assume alpha-beta currents are passed in
    
    // Step 2: Park Transform - Convert αβ to dq
    park_transform(i_alpha, i_beta, theta_elec, 
                   &foc_state.id_measured, &foc_state.iq_measured);
    
    // Step 3: PI Current Control - Iq loop (torque control)
    float iq_error = foc_state.iq_target - foc_state.iq_measured;
    foc_state.vq = pid_update(&iq_pid, iq_error, dt_seconds);
    
    // Step 4: PI Current Control - Id loop (flux control)
    float id_error = foc_state.id_target - foc_state.id_measured;
    foc_state.vd = pid_update(&id_pid, id_error, dt_seconds);
    
    // Step 5: Inverse Park Transform - Convert dq to αβ
    inv_park_transform(foc_state.vd, foc_state.vq, theta_elec,
                       &foc_state.vout_alpha, &foc_state.vout_beta);
    
    // Step 6: SVPWM Modulation - Convert αβ to 3-phase duty cycles
    // Note: SVPWM is called from motor_control module
}

foc_state_t foc_get_state(void) {
    return foc_state;
}

void foc_set_iq_target(float iq_amps) {
    // Implement torque slew rate limiting for safety
    static float last_iq_target = 0.0f;
    float max_change = TORQUE_SLEW_RATE;  // Amps per millisecond
    
    float change = iq_amps - last_iq_target;
    if (change > max_change) {
        iq_amps = last_iq_target + max_change;
    } else if (change < -max_change) {
        iq_amps = last_iq_target - max_change;
    }
    
    foc_state.iq_target = iq_amps;
    last_iq_target = iq_amps;
}

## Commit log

2025-12-26 added images and BOM
    [BOM WheelBase + Steering Wheel.csv, BOM-WheelBase.csv, BOM_Wheel.csv]
2025-12-26 added step,stl and source 3d model file
    [Corner screw support.STL, Motor attachment.STL, ODSEC SUPPORT.STL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]
2025-12-27 Added BOM
    Added BOM
2025-12-27 updated BOM again :(
    [BOM WheelBase + Steering Wheel.csv, BOM-WheelBase.csv, BOM_Wheel.csv]
2025-12-27 created code for Pico 2 of the wheel
2025-12-28 added the software for the pico 2 of the wheel base
2026-03-31 added pcb files (kicad 10)
    [bldc motor driver.kicad_pcb, bldc motor driver.kicad_sch, bom.csv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]
2026-03-31 added software for BLDC MOTOR DRIVER PCB
    [BOM TOTAL.csv, BOM-WheelBase.csv, BOM_Wheel.csv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]
